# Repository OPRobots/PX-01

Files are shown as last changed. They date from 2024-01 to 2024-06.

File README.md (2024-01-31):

# PX-01 Linefollower

Robot siguelineas modular. Está pensado para tener un diseño sencillo a la par que lo mas competitivo posible. Con 16 sensores IR, succión y motores de gran poder.

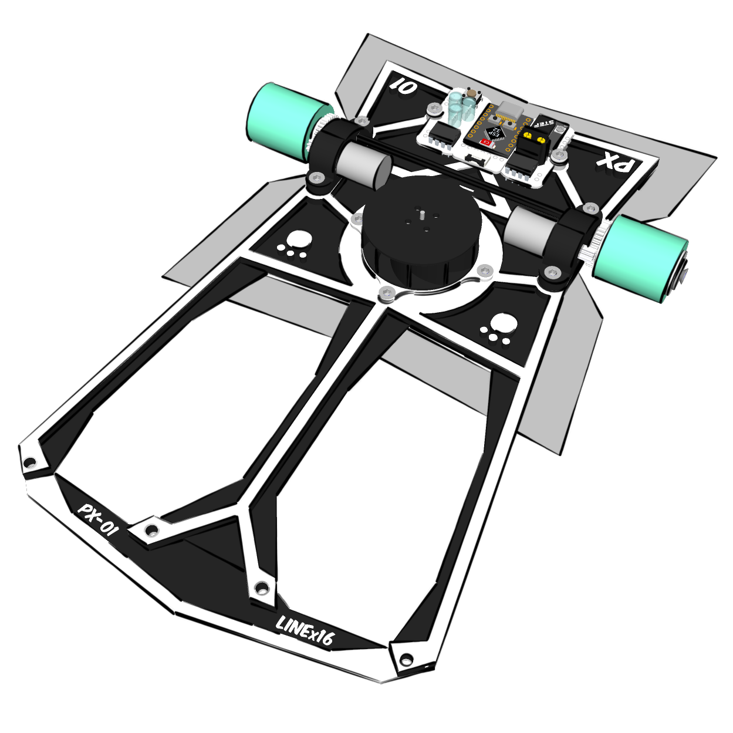
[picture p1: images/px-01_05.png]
PX-01


[Más información y conjunta](http://oprobots.github.io/tienda/kits/px-01/ "Más información y conjunta")

*en construcción*

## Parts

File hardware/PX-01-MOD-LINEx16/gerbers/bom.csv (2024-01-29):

Designator | Footprint | Quantity | Value | LCSC Part #
AUX_FLEX1, FLEX_MORRO1 | TE_0-1734839-7_1x07-1MP_P0.5mm_Horizontal | 2 | Conn_01x07 | C388693
C1, C3 | 0805 | 2 | 10uF | C380331
C2, C4 | 0805 | 2 | 0.1uF | C2847428
MUX1, MUX2 | MUX_CD4051B | 2 | CD4051B | C3007951
R1, R10, R13, R16, R19, R22, R4, R7 | 0805 | 8 | 45 | C3017827
R11, R12, R14, R15, R17, R18, R2, R20, R21, R23, R24, R3, R5, R6, R8, R9 | 0805 | 16 | 10k | C17414
S1, S10, S11, S12, S13, S14, S15, S16, S2, S3, S4, S5, S6, S7, S8, S9 | ITR8307_SMD | 16 | ~ | C81632

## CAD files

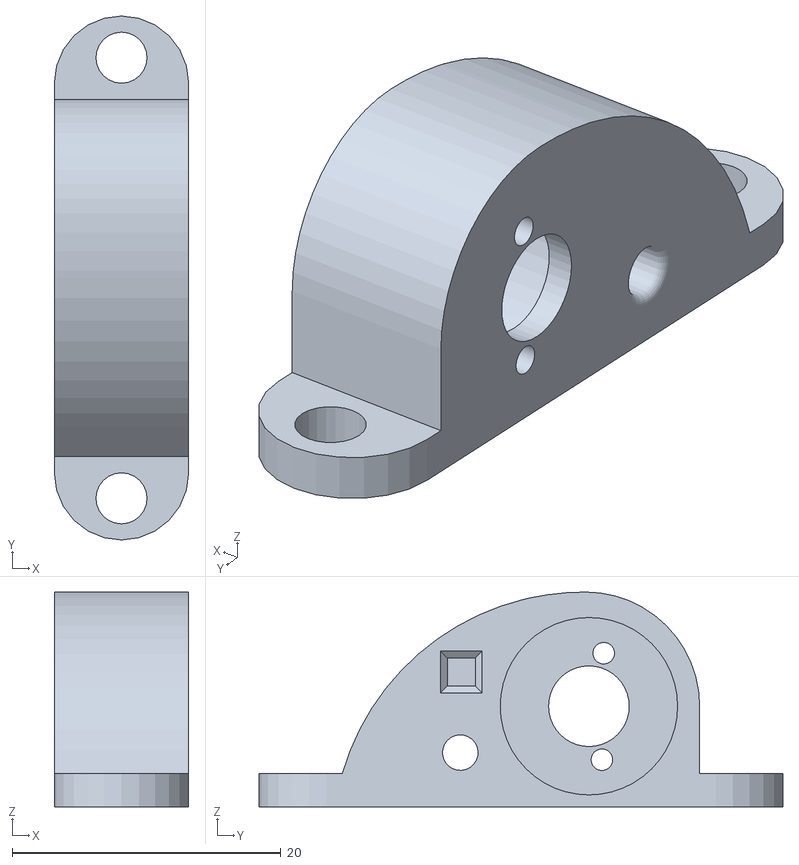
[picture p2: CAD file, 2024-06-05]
3d_model/stl_files/Bracket_derecho.stl
10.0 x 39.0 x 16.0

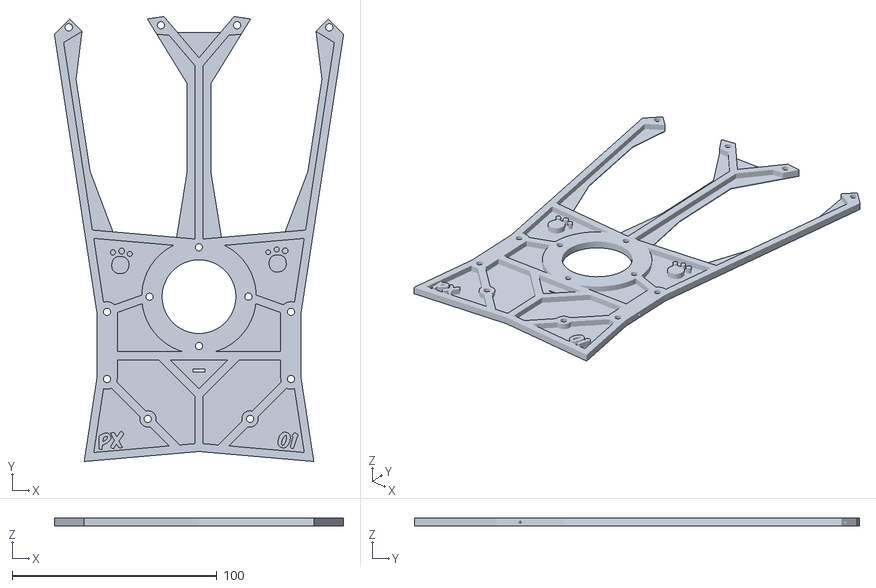
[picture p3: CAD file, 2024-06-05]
3d_model/stl_files/Chasis.stl
141.3 x 217.3 x 3.71

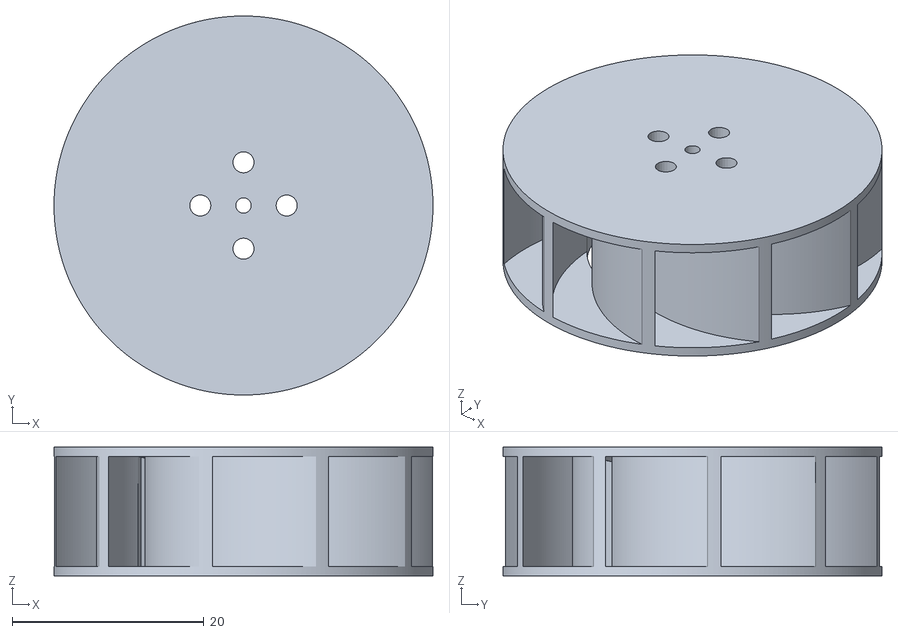
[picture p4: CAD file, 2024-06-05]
3d_model/stl_files/Ventilador.stl
39.5 x 39.5 x 13.4

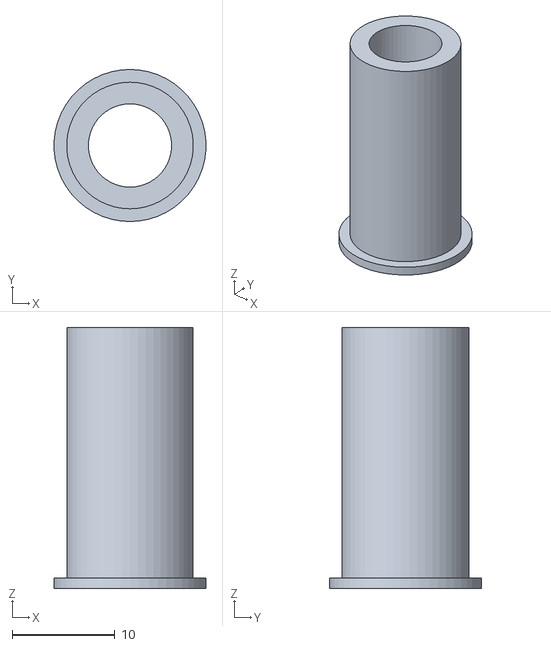
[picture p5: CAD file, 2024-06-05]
3d_model/stl_files/Llanta.stl
14.8 x 14.8 x 25.4

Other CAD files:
3d_model/stl_files/Bracket_izquierdo.stl

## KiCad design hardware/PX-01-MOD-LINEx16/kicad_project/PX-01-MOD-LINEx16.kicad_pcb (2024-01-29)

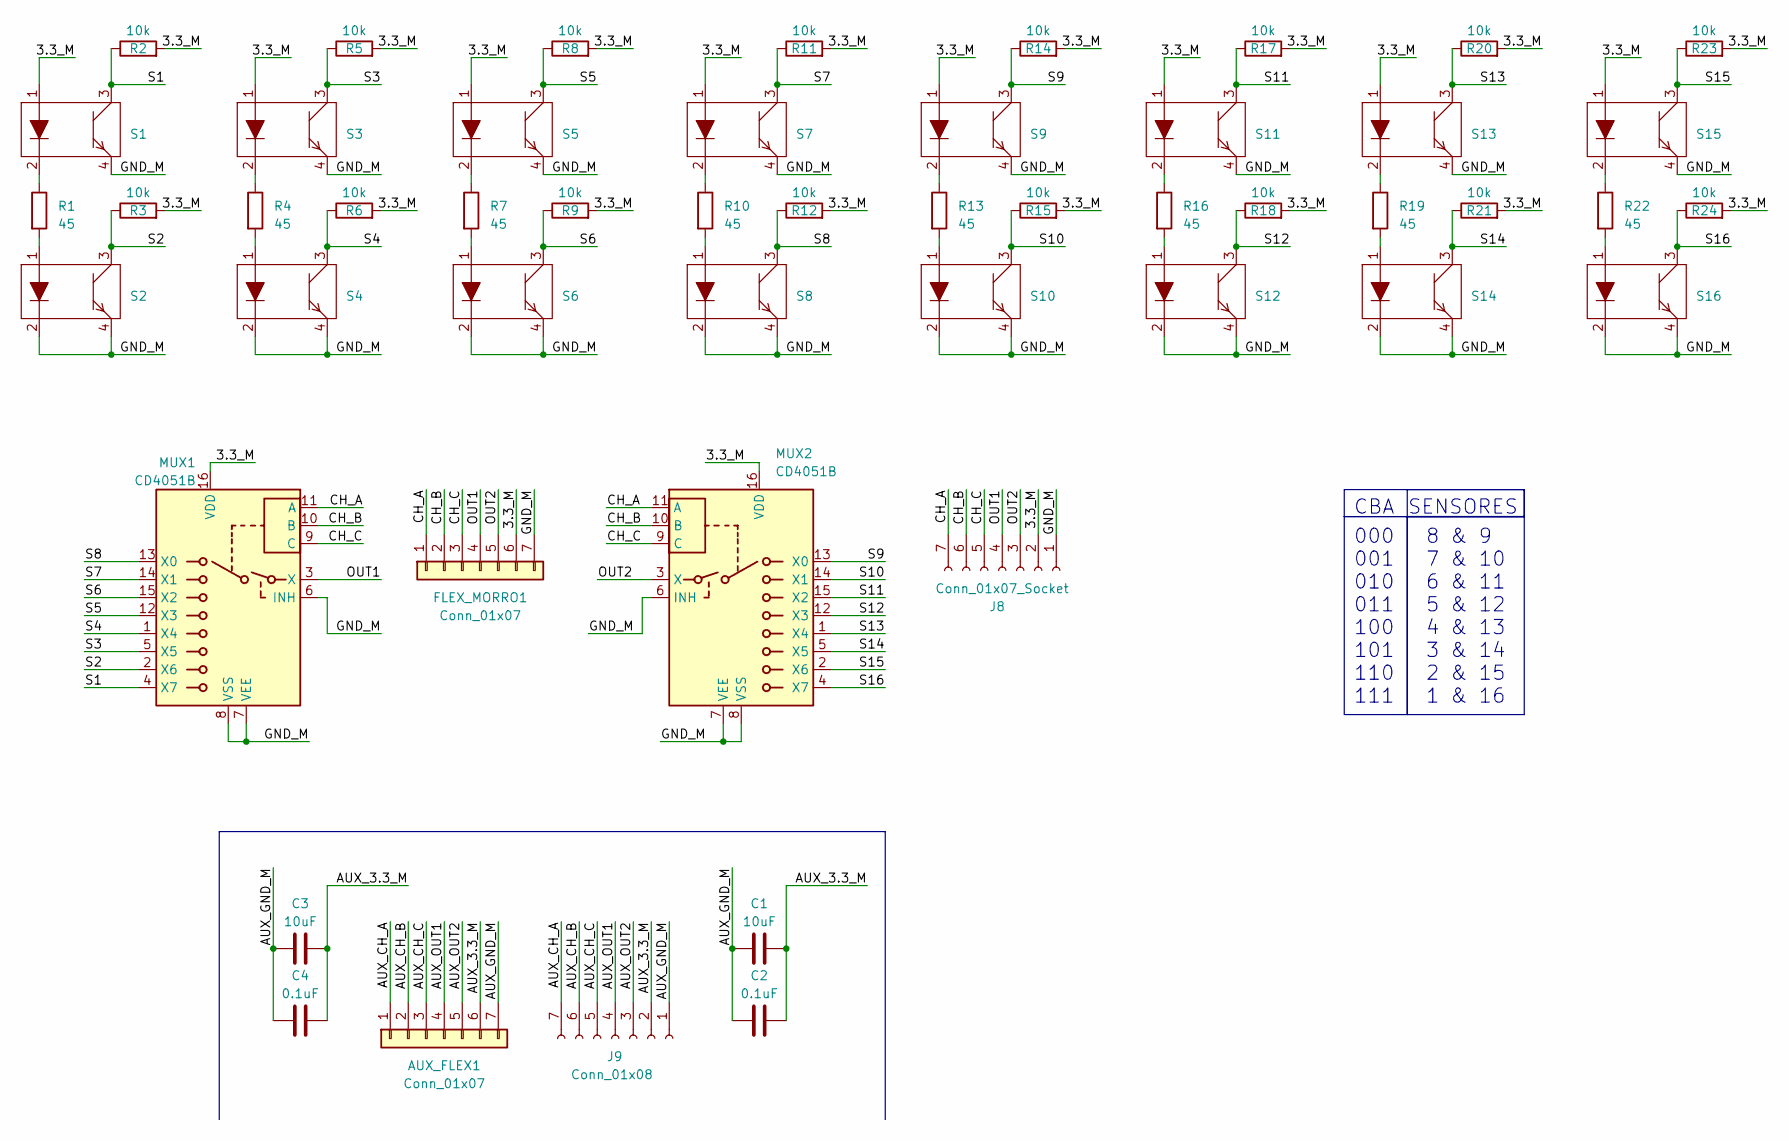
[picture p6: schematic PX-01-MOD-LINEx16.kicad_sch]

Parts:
AUX_FLEX1: Conn_01x07; TE_0-1734839-7_1x07-1MP_P0.5mm_Horizontal; LCSC Part # C388693
C1, C3: 10uF; C_0805_2012Metric_Pad1.18x1.45mm_HandSolder; LCSC Part # C380331
C2, C4: 0.1uF; C_0805_2012Metric_Pad1.18x1.45mm_HandSolder; LCSC Part # C2847428
FLEX_MORRO1: Conn_01x07; TE_0-1734839-7_1x07-1MP_P0.5mm_Horizontal; LCSC Part # C388693
J8: Conn_01x07_Socket; PinHeader_1x07_P2.54mm_Vertical
J9: Conn_01x08; PinHeader_1x07_P2.54mm_Vertical
MUX1, MUX2: CD4051B; MUX_CD4051B; LCSC Part # C3007951
R1, R4, R7, R10, R13, R16, R19, R22: 45; R_0805_2012Metric_Pad1.20x1.40mm_HandSolder; LCSC Part # C3017827
R2, R3, R5, R6, R8, R9, R11, R12, R14, R15, R17, R18, R20, R21, R23, R24: 10k; R_0805_2012Metric_Pad1.20x1.40mm_HandSolder; LCSC Part # C17414
S1, S2, S3, S4, S5, S6, S7, S8, S9, S10, S11, S12, S13, S14, S15, S16: ITR8307_SMD; LCSC Part # C81632

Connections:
/3.3_M: FLEX_MORRO1.6, J8.2, MUX1.16 (VDD), MUX2.16 (VDD), R2.2, R3.2, R5.2, R6.2, R8.2, R9.2, R11.2, R12.2, R14.2, R15.2, R17.2, R18.2, R20.2, R21.2, R23.2, R24.2, S1.1, S3.1, S5.1, S7.1, S9.1, S11.1, S13.1, S15.1
/AUX_3.3_M: AUX_FLEX1.6, C1.1, C2.1, C3.1, C4.1, J9.2
/AUX_CH_A: AUX_FLEX1.1, J9.7
/AUX_CH_B: AUX_FLEX1.2, J9.6
/AUX_CH_C: AUX_FLEX1.3, J9.5
/AUX_GND_M: AUX_FLEX1.7, C1.2, C2.2, C3.2, C4.2, J9.1
/AUX_OUT1: AUX_FLEX1.4, J9.4
/AUX_OUT2: AUX_FLEX1.5, J9.3
/CH_A: FLEX_MORRO1.1, J8.7, MUX1.11 (A), MUX2.11 (A)
/CH_B: FLEX_MORRO1.2, J8.6, MUX1.10 (B), MUX2.10 (B)
/CH_C: FLEX_MORRO1.3, J8.5, MUX1.9 (C), MUX2.9 (C)
/GND_M: FLEX_MORRO1.7, J8.1, MUX1.6 (INH), MUX1.7 (VEE), MUX1.8 (VSS), MUX2.6 (INH), MUX2.7 (VEE), MUX2.8 (VSS), S1.4, S2.2, S2.4, S3.4, S4.2, S4.4, S5.4, S6.2, S6.4, S7.4, S8.2, S8.4, S9.4, S10.2, S10.4, S11.4, S12.2, S12.4, S13.4, S14.2, S14.4, S15.4, S16.2, S16.4
/OUT1: FLEX_MORRO1.4, J8.4, MUX1.3 (X)
/OUT2: FLEX_MORRO1.5, J8.3, MUX2.3 (X)
/S1: MUX1.4 (X7), R2.1, S1.3
/S2: MUX1.2 (X6), R3.1, S2.3
/S3: MUX1.5 (X5), R5.1, S3.3
/S4: MUX1.1 (X4), R6.1, S4.3
/S5: MUX1.12 (X3), R8.1, S5.3
/S6: MUX1.15 (X2), R9.1, S6.3
/S7: MUX1.14 (X1), R11.1, S7.3
/S8: MUX1.13 (X0), R12.1, S8.3
/S9: MUX2.13 (X0), R14.1, S9.3
/S10: MUX2.14 (X1), R15.1, S10.3
/S11: MUX2.15 (X2), R17.1, S11.3
/S12: MUX2.12 (X3), R18.1, S12.3
/S13: MUX2.1 (X4), R20.1, S13.3
/S14: MUX2.5 (X5), R21.1, S14.3
/S15: MUX2.2 (X6), R23.1, S15.3
/S16: MUX2.4 (X7), R24.1, S16.3
unnamed: R1.1, S1.2
unnamed: R1.2, S2.1
unnamed: R4.1, S3.2
unnamed: R4.2, S4.1
unnamed: R7.1, S5.2
unnamed: R7.2, S6.1
unnamed: R10.1, S7.2
unnamed: R10.2, S8.1
unnamed: R13.1, S9.2
unnamed: R13.2, S10.1
unnamed: R16.1, S11.2
unnamed: R16.2, S12.1
unnamed: R19.1, S13.2
unnamed: R19.2, S14.1
unnamed: R22.1, S15.2
unnamed: R22.2, S16.1

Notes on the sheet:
CBA
SENSORES
8 & 9 7 & 10 6 & 11 5 & 12 4 & 13 3 & 14 2 & 15 1 & 16
000 001 010 011 100 101 110 111

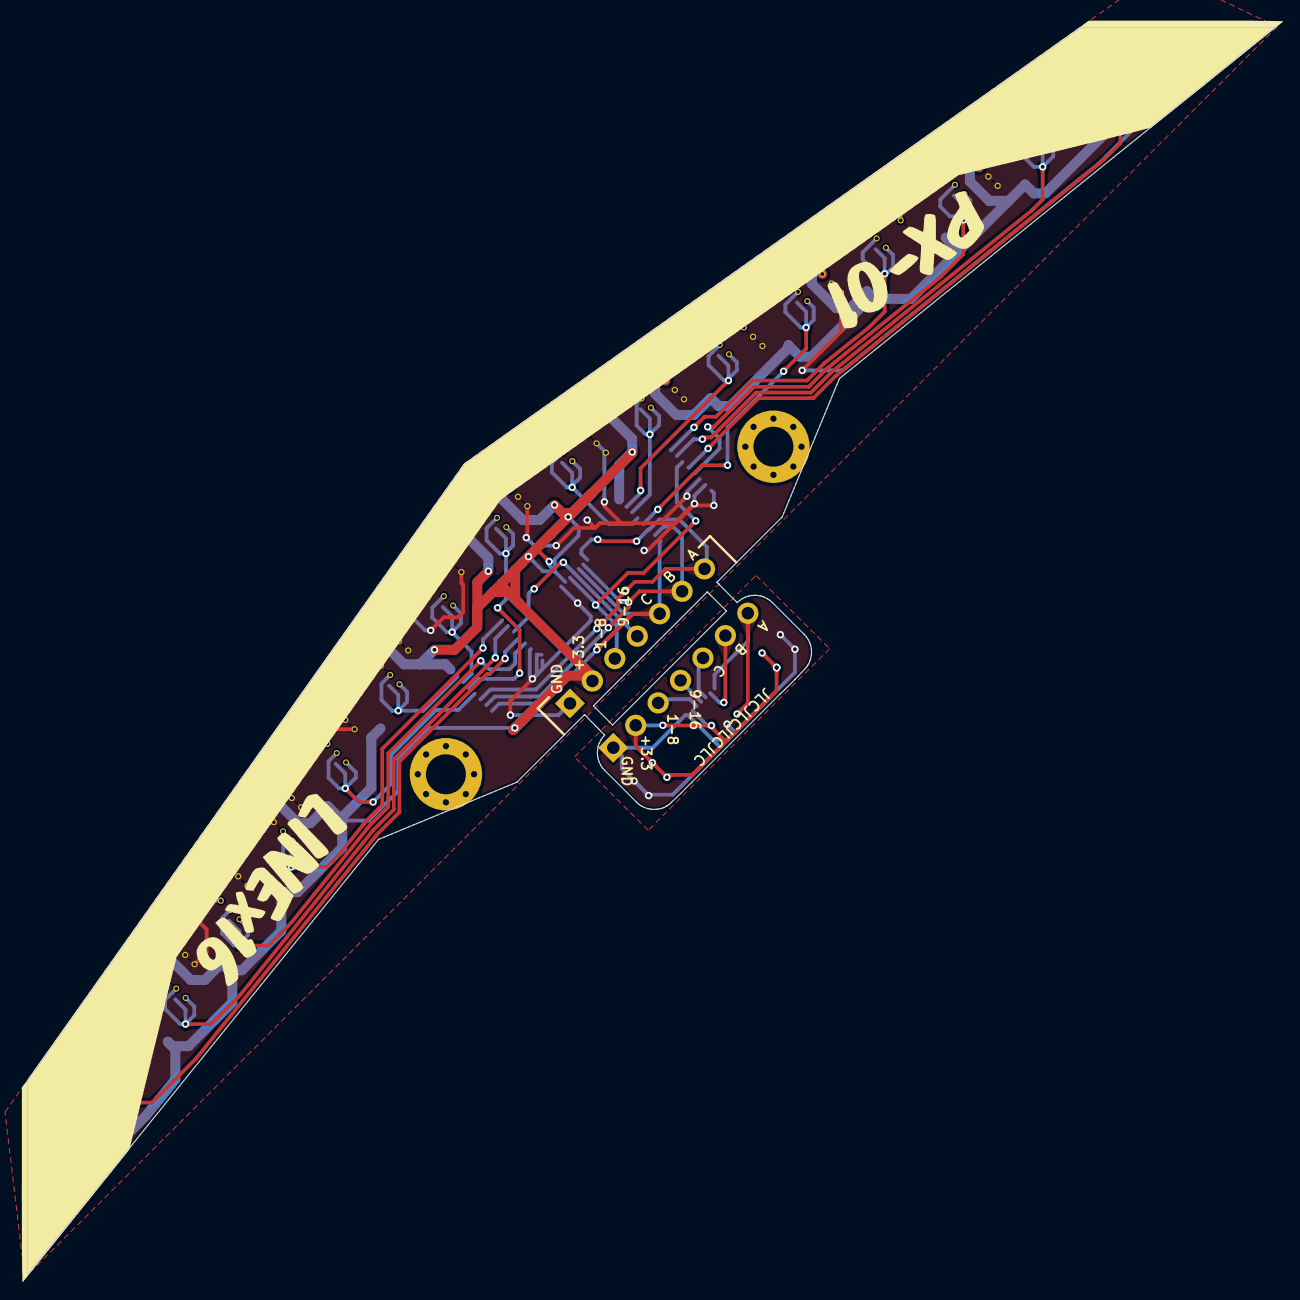
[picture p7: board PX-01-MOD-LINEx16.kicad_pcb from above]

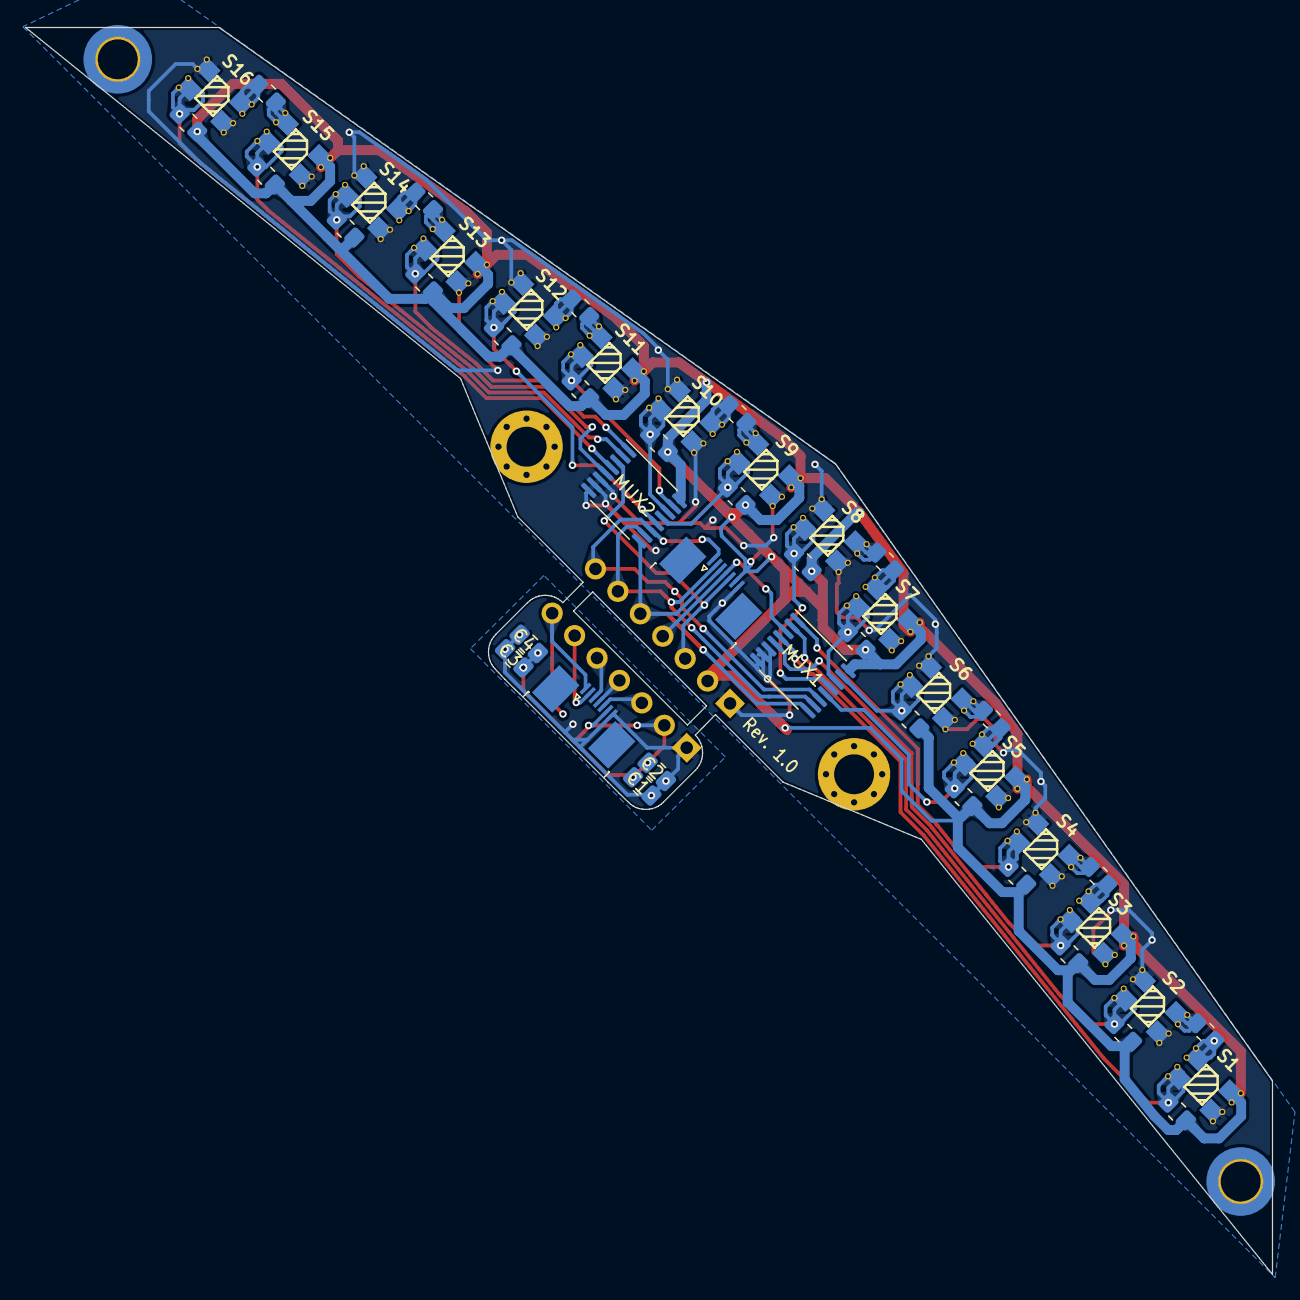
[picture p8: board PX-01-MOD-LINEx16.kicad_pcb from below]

Board: 2 copper layers, 99.9 x 99.9 mm, 50 parts (49 on the bottom side), 46 nets.

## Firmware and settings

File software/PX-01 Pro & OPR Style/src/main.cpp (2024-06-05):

#include <Arduino.h>

#include <config.h>
#include <control.h>
#include <menu.h>
#include <pinout.h>
#include <sensors.h>
#include <utils.h>

bool race_started = false;
long race_started_ms = 0;

void setup() {
  init_components();
  calibrate_sensors();
}

void loop() {

  if (!is_race_started()) {
    BTN_STATES btn_state = get_btn_pressed_state();
    if (btn_state == BTN_PRESSING && get_btn_pressing_ms() >= 250) {
      clear_led(RGB_LEFT);
      clear_led(RGB_TOP);
      clear_led(RGB_RIGHT);
      while (btn_state == BTN_PRESSING) {
        blink_led(RGB_RIGHT, 0, 0, 50, 125);
        blink_led(RGB_TOP, 0, 0, 50, 125);
        blink_led(RGB_LEFT, 0, 0, 50, 125);
        btn_state = get_btn_pressed_state();
      }
    } else {
      handle_menu(btn_state);
    }

    if (btn_state == BTN_LONG_PRESSED) {
      set_led(RGB_LEFT, 0, 0, 50);
      set_led(RGB_TOP, 0, 0, 50);
      set_led(RGB_RIGHT, 0, 0, 50);
      long starting_ms = millis();
      while (millis() < (starting_ms + get_ms_start())) {
        if (get_ms_start() > 3000 && millis() - starting_ms < get_ms_start() - 3000) {
          blink_led(RGB_RIGHT, 0, 0, 50, 500);
          blink_led(RGB_TOP, 0, 0, 50, 500);
          blink_led(RGB_LEFT, 0, 0, 50, 500);
        } else {
          if (millis() - starting_ms < get_ms_start() - 2000) {
            set_led(RGB_LEFT, 0, 0, 50);
            set_led(RGB_TOP, 0, 0, 50);
            set_led(RGB_RIGHT, 0, 0, 50);
          } else if (millis() - starting_ms < get_ms_start() - 1000) {
            set_led(RGB_RIGHT, 0, 0, 50);
            set_led(RGB_LEFT, 0, 0, 50);
            clear_led(RGB_TOP);
          } else {
            set_led(RGB_TOP, 0, 0, 50);
            clear_led(RGB_LEFT);
            clear_led(RGB_RIGHT);
            if (get_base_fan_speed() != 0) {
              set_fan_speed(get_base_fan_speed() * 0.85f);
            }
            set_race_starting(true);
            initial_control_loop();
          }
        }
      }
      clear_led(RGB_LEFT);
      clear_led(RGB_TOP);
      clear_led(RGB_RIGHT);
      set_race_started(true);
    }
  } else {
    control_loop();
#ifdef MODE_TEST
    if ((millis() - get_race_started_ms()) >= TEST_DURATION_MS) {
      set_fan_speed(0);
      set_motors_speed(0, 0);
      set_race_started(false);
    }
#endif
  }
}

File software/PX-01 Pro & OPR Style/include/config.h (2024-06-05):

#ifndef CONFIG_H
#define CONFIG_H

#include <Arduino.h>
#include <motors.h>
#include <pinout.h>

/**
 * @brief Indica el modo de funcionamiento del robot.
 *
 */
#define MODE_TEST 1
// #define MODE_RACE 2

/**
 * @brief Indica si la línea a seguir es blanca o negra.
 * Este control se usa para aplicar un filtro en la detección de la línea.
 * 
 */
// #define LINE_WHITE 0
#define LINE_BLACK 1

/**
 * @brief Tiempo de espera para iniciar carrera después de pulsar el botón.
 *
 */
#define START_TEST_MS 3000
#define START_RACE_MS 5000

/**
 * @brief Tiempo máximo de ejecución en modo prueba (MODE_TEST).
 * Después de este tiempo, el robot se detendrá automáticamente.
 * 
 */
#define TEST_DURATION_MS 5000

/**
 * @brief Define el tiempo de espera entre ejecuciones del bucle de control en microsegundos.
 *
 */
#define CONTROL_LOOP_US 1000

/**
 * @brief Tiempo de calibración de sensores.
 *
 */
#define SENSORS_CALIBRATION_MS 3000

/**
 * @brief Configuración de Velocidad y Aceleración.
 * Dispone de varios menús para seleccionar la velocidad y aceleración del robot.
 * 
 */
#define MENU_1_BASE_SPEED 15
#define MENU_1_ACCEL_SPEED 60
#define MENU_1_BASE_FAN_SPEED 0

#define MENU_2_BASE_SPEED 20
#define MENU_2_ACCEL_SPEED 60
#define MENU_2_BASE_FAN_SPEED 50

#define MENU_3_BASE_SPEED 30
#define MENU_3_ACCEL_SPEED 60
#define MENU_3_BASE_FAN_SPEED 70

/**
 * @brief Constantes del controlador PID.
 *
 */
#define PID_KP 0.2
#define PID_KD 0.80

void init_components();
long get_ms_start();

#endif

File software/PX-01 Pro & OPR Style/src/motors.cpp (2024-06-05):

#include <motors.h>

/**
 * @brief Inicializa el timer controlador de los motores
 *
 */
void init_motors() {
  // Configuración de los canales PWM del Timer
  ledcSetup(PWM_MOTOR_RIGHT_A, PWM_MOTORS_HZ, PWM_MOTORS_RESOLUTION);
  ledcSetup(PWM_MOTOR_RIGHT_B, PWM_MOTORS_HZ, PWM_MOTORS_RESOLUTION);
  ledcSetup(PWM_MOTOR_LEFT_A, PWM_MOTORS_HZ, PWM_MOTORS_RESOLUTION);
  ledcSetup(PWM_MOTOR_LEFT_B, PWM_MOTORS_HZ, PWM_MOTORS_RESOLUTION);
  ledcSetup(PWM_SUCTION, PWM_SUCTION_HZ, PWM_SUCTION_RESOLUTION);

  // Asignación de los pines a los canales PWM
  ledcAttachPin(MOTOR_RIGHT_A, PWM_MOTOR_RIGHT_A);
  ledcAttachPin(MOTOR_RIGHT_B, PWM_MOTOR_RIGHT_B);
  ledcAttachPin(MOTOR_LEFT_A, PWM_MOTOR_LEFT_A);
  ledcAttachPin(MOTOR_LEFT_B, PWM_MOTOR_LEFT_B);
  ledcAttachPin(MOTOR_SUCTION, PWM_SUCTION);

  // Establece el valor inicial de los canales PWM
  ledcWrite(PWM_MOTOR_RIGHT_A, PWM_MOTORS_MIN);
  ledcWrite(PWM_MOTOR_RIGHT_B, PWM_MOTORS_MIN);
  ledcWrite(PWM_MOTOR_LEFT_A, PWM_MOTORS_MIN);
  ledcWrite(PWM_MOTOR_LEFT_B, PWM_MOTORS_MIN);
  ledcWrite(PWM_SUCTION, PWM_SUCTION_MIN);

  // Tiempo de espera para inicialización del ESC; se puede comentar si se espera manualmente (calibrando, ajustando velocidad, etc.)
  // delay(5000);
}

/**
 * @brief Establece la velocidad de los motores
 *
 * @param velI Velocidad del motor izquierdo 0-100%
 * @param velD Velocidad del motor derecho 0-100%
 */
void set_motors_speed(float velI, float velD) {
  if (velI > 100) {
    velI = 100;
  } else if (velI < -100) {
    velI = -100;
  }

  if (is_race_started() || is_race_starting() || millis() - get_race_stopped_ms() < 1000) {
    if (velI > 0) {
      ledcWrite(PWM_MOTOR_LEFT_A, PWM_MOTORS_MAX- (PWM_MOTORS_MAX * velI / 100));
      ledcWrite(PWM_MOTOR_LEFT_B, PWM_MOTORS_MAX );
    } else {
      ledcWrite(PWM_MOTOR_LEFT_A, PWM_MOTORS_MAX );
      ledcWrite(PWM_MOTOR_LEFT_B, PWM_MOTORS_MAX- (PWM_MOTORS_MAX * abs(velI) / 100));
    }
  } else {
    ledcWrite(PWM_MOTOR_LEFT_A, PWM_MOTORS_MIN);
    ledcWrite(PWM_MOTOR_LEFT_B, PWM_MOTORS_MIN);
  }

  if (velD > 100) {
    velD = 100;
  } else if (velD < -100) {
    velD = -100;
  }

  if (is_race_started() || is_race_starting() || millis() - get_race_stopped_ms() < 1000) {
    if (velD > 0) {
      ledcWrite(PWM_MOTOR_RIGHT_A, PWM_MOTORS_MAX );
      ledcWrite(PWM_MOTOR_RIGHT_B, PWM_MOTORS_MAX- (PWM_MOTORS_MAX * velD / 100));
    } else {
      ledcWrite(PWM_MOTOR_RIGHT_A, PWM_MOTORS_MAX- (PWM_MOTORS_MAX * abs(velD) / 100));
      ledcWrite(PWM_MOTOR_RIGHT_B, PWM_MOTORS_MAX );
    }
  } else {
    ledcWrite(PWM_MOTOR_RIGHT_A, PWM_MOTORS_MIN);
    ledcWrite(PWM_MOTOR_RIGHT_B, PWM_MOTORS_MIN);
  }
}

/**
 * @brief Establece la velocidad del ventilador
 *
 * @param vel Velocidad del ventilador 0-100%
 */
void set_fan_speed(int vel) {
  if (vel != 0) {
    ledcWrite(PWM_SUCTION, map(vel, 0, 100, PWM_SUCTION_MIN, PWM_SUCTION_MAX));
  } else {
    ledcWrite(PWM_SUCTION, PWM_SUCTION_MIN);
  }
}

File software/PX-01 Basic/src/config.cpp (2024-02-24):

#include <config.h>

/**
 * @brief Inicializa los componentes del robot.
 *
 */
void init_components() {
  Serial.begin(115200);

  pinMode(NEOPIXEL, OUTPUT);
  pinMode(MOD_START, INPUT_PULLDOWN);
  pinMode(BTN_1, INPUT_PULLDOWN);

  pinMode(SENSOR_1, OUTPUT);
  pinMode(SENSOR_2, OUTPUT);
  pinMode(MUX_C, OUTPUT);
  pinMode(MUX_B, OUTPUT);
  pinMode(MUX_A, OUTPUT);

  pinMode(MOTOR_RIGHT_A, OUTPUT);
  pinMode(MOTOR_RIGHT_B, OUTPUT);
  pinMode(MOTOR_LEFT_A, OUTPUT);
  pinMode(MOTOR_LEFT_B, OUTPUT);
  digitalWrite(MOTOR_RIGHT_A, HIGH);
  digitalWrite(MOTOR_RIGHT_B, HIGH);
  digitalWrite(MOTOR_LEFT_A, HIGH);
  digitalWrite(MOTOR_LEFT_B, HIGH);

  init_motors();
}

/**
 * @brief Obtiene el tiempo de espera para iniciar carrera después de pulsar el botón.
 *
 * @return long Tiempo de espera en ms.
 */
long get_ms_start() {
#ifdef MODE_RACE
  return START_RACE_MS;
#else
  return START_TEST_MS;
#endif
}

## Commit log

2024-01-15 Añade submódulo de PX-CORE
2024-01-15 Añade estructura inicial de carpetas
2024-01-15 Añade proyectos KiCad de PX-01-MOD-LINEx16 y PX-01-MOD-SUCTION-FAN
    [PX-01-MOD-LINEx16.kicad_pcb, PX-01-MOD-LINEx16.kicad_sch, PX-01-MOD-SUCTION-FAN.kicad_pcb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]
2024-01-15 Actualiza submodules de PX-CORE y custom_libraries
2024-01-17 Añade Revisión y Modelos 3D
    [PX-01-MOD-LINEx16.kicad_pcb, PX-01-MOD-LINEx16.kicad_sch]
2024-01-25 Actualiza Silkscreen para PCB en negro y añade referencias LCSC
    [PX-01-MOD-LINEx16.kicad_pcb, PX-01-MOD-LINEx16.kicad_sch]
2024-01-25 Añade gerbers y actualiza flex a 7P. Cambia la referencia de algunos componentes
    [PX-01-MOD-LINEx16.kicad_pcb, PX-01-MOD-LINEx16.kicad_sch, bom.csv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]
2024-01-29 Actualiza hardware de PX-CORE
2024-01-29 Añade BOM para PX-01-MOD-LINEx16
2024-02-09 Añade programa para Pro y OPR Style
2024-02-20 Cambia pequeños ajustes de configuracion, y corrige logica del boton
    [config.cpp, config.h, main.cpp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]
2024-02-24 Actualiza la PX-CORE a la Rev. 1.0
2024-02-24 Añade desbloqueo de motores al iniciar y al detenerse
2024-02-24 Añade código para modelo Basic
2024-02-24 Actualiza Workspaces para Pro y Basic
2024-04-01 Cambia sentido de motores y ajusta velocidades de menu
2024-04-04 Corrige workspace de Pro & OPR Style
2024-04-04 Corrige aceleración y añade corrección de posición inicial
    [config.h, control.cpp, main.cpp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]
2024-06-05 Cambia la configuracion de velocidad en config.h
2024-06-05 Añade los STLs
    [Bracket_derecho.stl, Bracket_izquierdo.stl, Chasis.stl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]
